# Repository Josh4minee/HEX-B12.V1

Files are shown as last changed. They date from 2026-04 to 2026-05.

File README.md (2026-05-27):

##
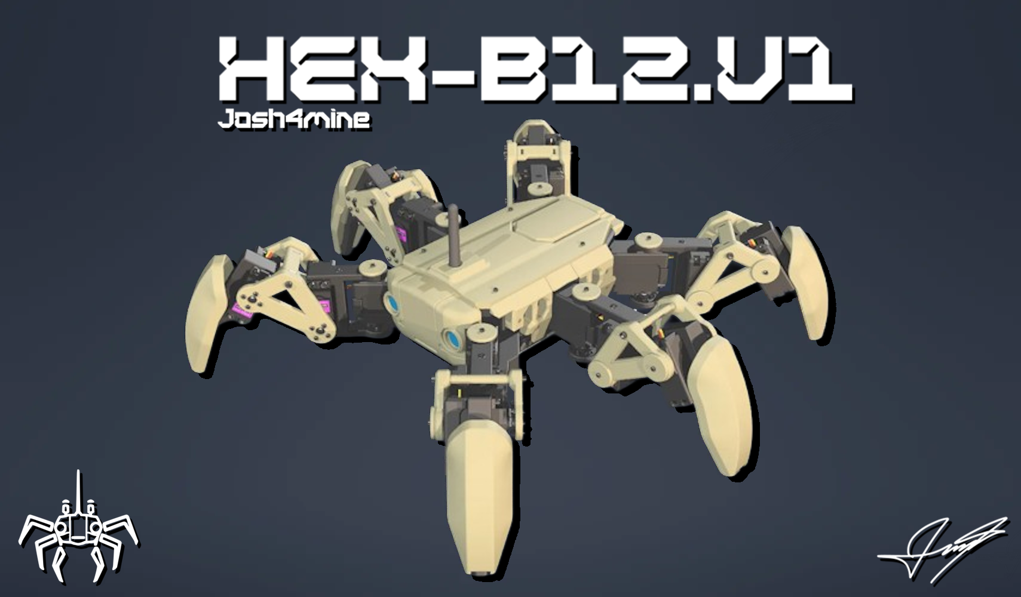
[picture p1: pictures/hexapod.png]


# HEX-B12.V1
HEX-B12.V120 is a custom-designed hexapod using MG996R servos. Its theme is based on the beloved bot B-12 from the popular video game [Stray](https://en.wikipedia.org/wiki/Stray_(video_game)). It is inspired by the Make Your Pet project and is powered by a custom inverse kinematics-based algorithm.

The mechanical part dimensions are inspired by the [Make Your Pet](https://www.makeyourpet.com/) Chipo project; everything else is custom-made by me.

# Information
Consult the following based on your needs:
- [Hexapod](#hexapod)
- [Remote](#remote)
- [Printing](#printing)
- [Wiring diagram](#wiring-diagram)
- [Hexapod Assembly](#hexapod-assembly)
- [Hexapod pictures and videos](#hexapod-pictures-and-videos)
- [Pre-powering on precautions](#pre-powering-on-precautions)
- [Remote Assembly](#remote-assembly)
- [How to use the remote](#how-to-use-the-remote)
- [Sources](#sources)
- [License](#license)

# Hexapod

Why I made this hexapod is because since I was young I have always wanted to build "stuff", making robots was always very appealing to me and this project is simpler than a quadruped yet just as fun for a beginner like me and I hope the people that come across this project like it! It is worth mentionning that this is also a college project hense why I have put so much time and effort on it in such a short ammount of time.

As per the title, this hexapod uses MG996R servos, this decision was made because of cost, any other servo is 3x to 4x the price of these ones.

The power system consists of one big 5200mAh 2S lipo battery for optimal opperation time, three UBECs for stable 7v to 5v conversion and one 10A manual reset fuse.

An arduino nano was used as the brains of this project simply because it was a requirement from my college and it is thanfully fast enough for its use case.

An [Adafruit PCA9685](https://learn.adafruit.com/16-channel-pwm-servo-driver/overview) servo driver was chosen to controll the huge amount fof servos this robot requires.

The nRF24L01+PA+LNA modules were chosen for wireless communication, the power emplified version was used for its antenna (to keep the resemblance of [B-12](https://stray.fandom.com/wiki/B-12)) and for its range.

Finally, relays were added for ease of use and safety, like only turning on the servos 5s after the battery is pluged in.

# Remote

The main reason the remote was made is because I did not want to work with bluetooth or web based control. 

Making a remote seemed more interesting anyways and it allowed me to design my very first custom PCB:

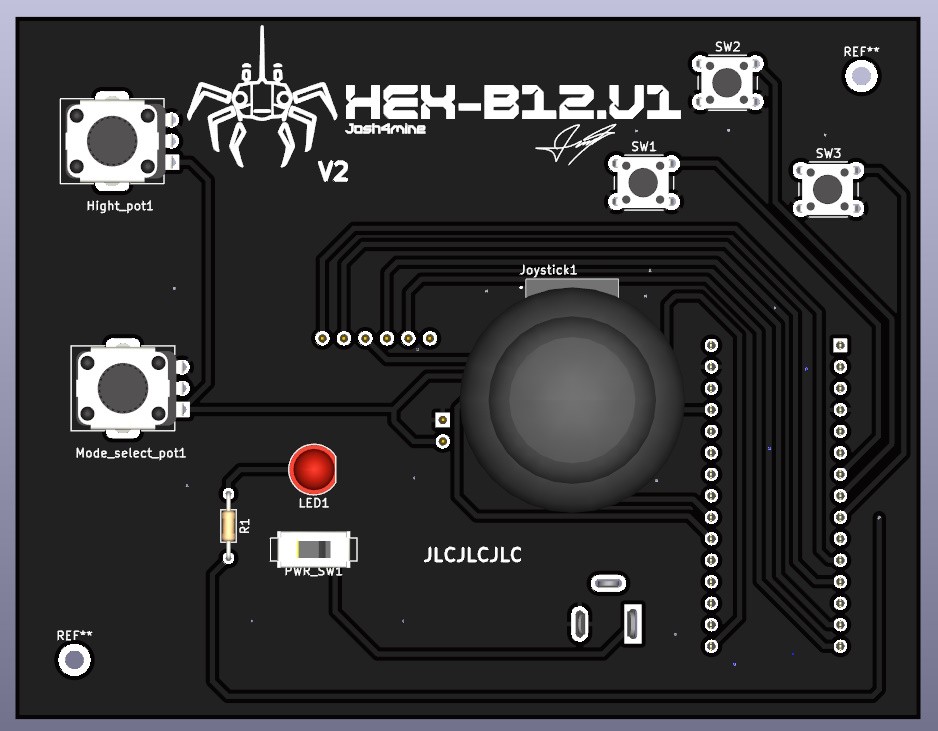
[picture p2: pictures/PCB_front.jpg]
  
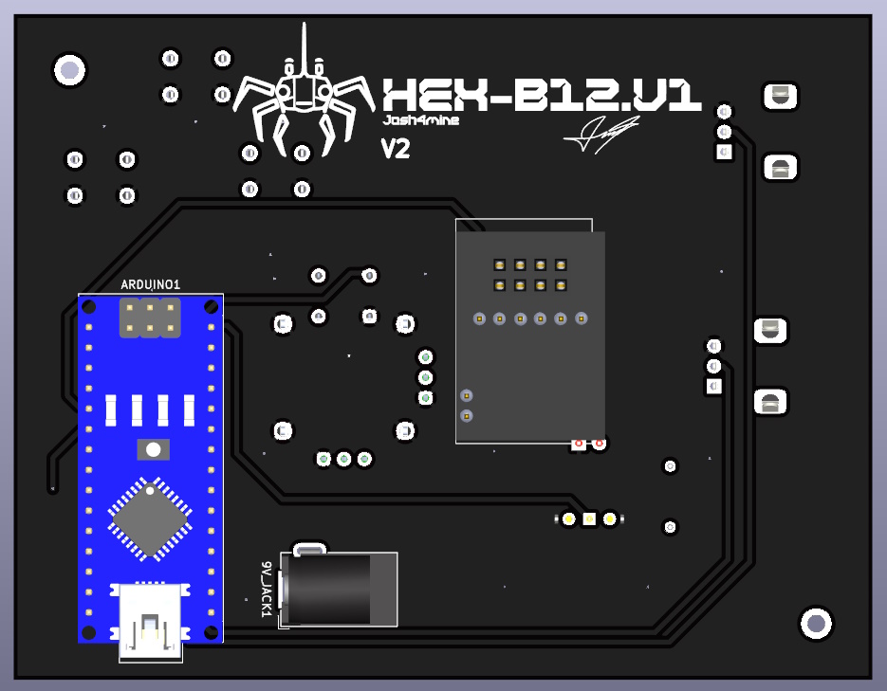
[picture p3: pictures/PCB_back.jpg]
  

I ended up making 2 versions because I tried to directly hook up an NRF module on the first version, this ended up failing to I just made a custom footprint for the NRF module power boards.

# Printing

The following are the settings used to print this hexapod:

- 15% grid infill everywhere, 0.28mm height and 3 walls on every part except for the 0.16mm servo shields to keep them smooth.
- Every STL file is pre-oriented and ready to print, the only parts requiring support material are the top plate, the shields, the coxa and femur horn parts, the guides. Any additional supports are not usefull.
- Printing the remote uses the same settings and the files are also pre-oriented, only the mid plate requires supports.
- The number of parts needed to be printed is indicated at the end of the names of every STL file.
- All STL files can be found the the [STL](./STL) folder.

# Wiring diagram

Here you can find the wiring diagram, component placements, and an IRL example of the completed build.
<div>
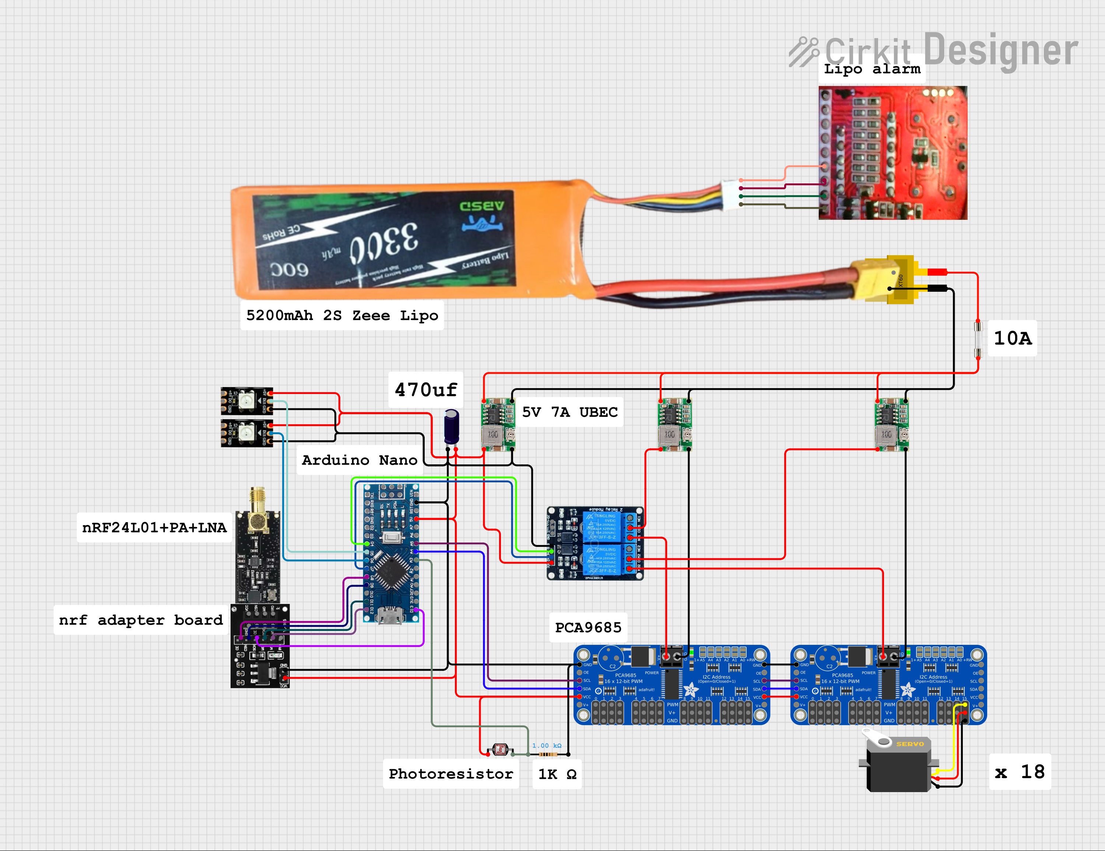
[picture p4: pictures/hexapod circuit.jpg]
  
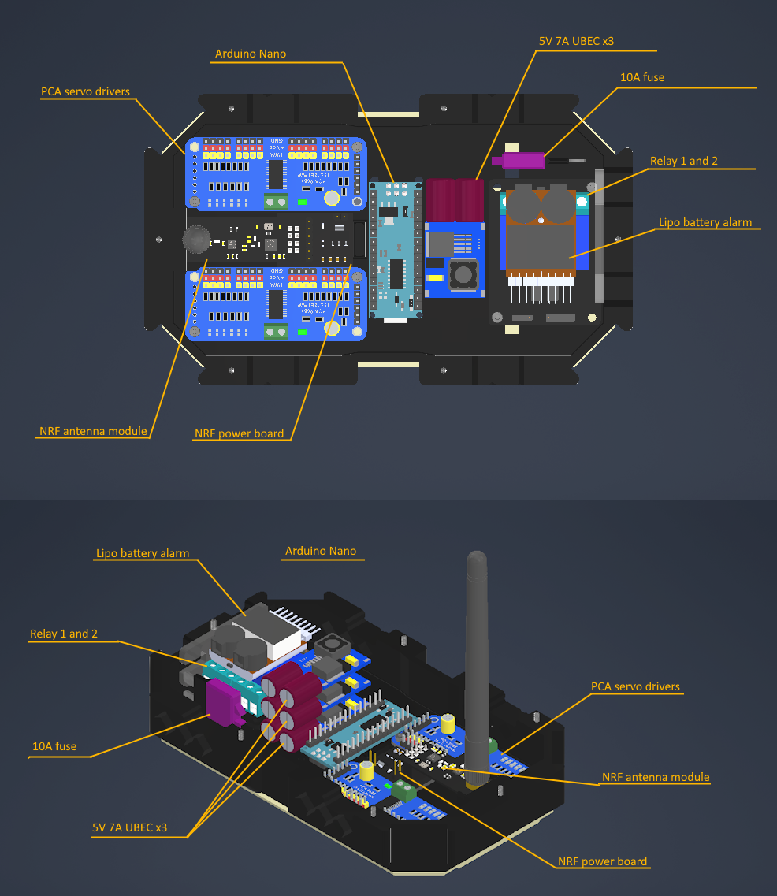
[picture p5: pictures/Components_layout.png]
  
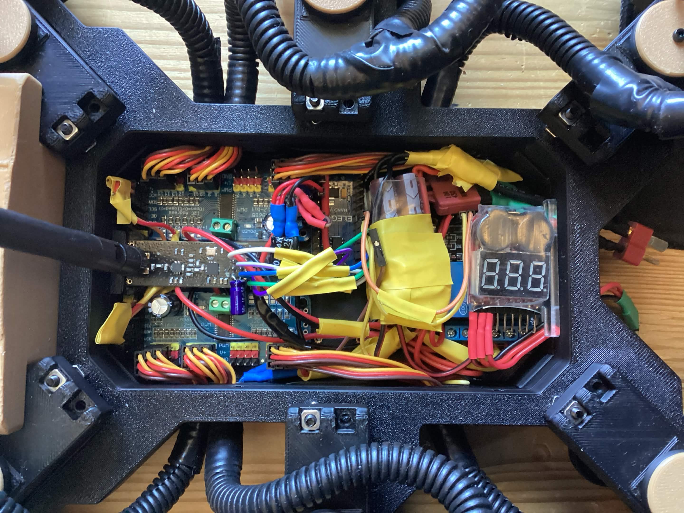
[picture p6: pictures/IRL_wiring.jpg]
  
<div>
  
# Hexapod assembly
- [Coxa](./pictures/coxa_page_1.jpg)
- [Femur](./pictures/femur_page_1.jpg)
- [Tibia](./pictures/tibia_page_1.jpg)
- [Leg](./pictures/LEG_left_page_1.jpg)
- [Mid Frame](./pictures/mid_frame_page_1.jpg)
- [Frame and Legs](./pictures/frampluslegs_page_1.jpg)
- [Hexapod](./pictures/hexapod_page_1.jpg)
- [Electronics Mounting](./pictures/electronics_mounting_page_1.jpg)
- [Servo pinouts](./pictures/servo_order.png)

**NOTE: ALL SERVOS MUST BE SET TO 90 PRIOR TO ANY ASSEMBLY**

**NOTE: KEEP IN MIND THAT 3 OF THESE LEGS ARE FLIPPED**

**NOTE: DO NOT FORGET THE 18 FRICTION CAP RINGS**

The above document provides a visual on how parts are assembled, to assemble this in real life you must follow the [Frame and Legs](./pictures/frampluslegs_page_1.jpg) and [Hexapod](./pictures/hexapod_page_1.jpg) technical drawings. The order of operations is very important here, so making sure proper understanding is acquired before continuing is mandatory.

For screw sizes needed:
- Every screw needed to attach a servo is M3 35mm.
- Every screw needed to clamp together femur/coxa parts is M3 25mm.
- Every screw that holds down the friction caps is M2 10mm.
- Every other screw is M2 8mm.
- Follow [this](./pictures/Hexapod_Heated_Insert_placements.png) diagram for M2 heat insert assembly.

Follow [this](./pictures/leg_orientations.png) technical drawing for proper leg orientation assembly.

It is very recommended to apply sillicone based grease between the friction caps and legs to prevent plastic wear.

# Hexapod pictures and videos

Here is what the robot should look like once fully assembled:
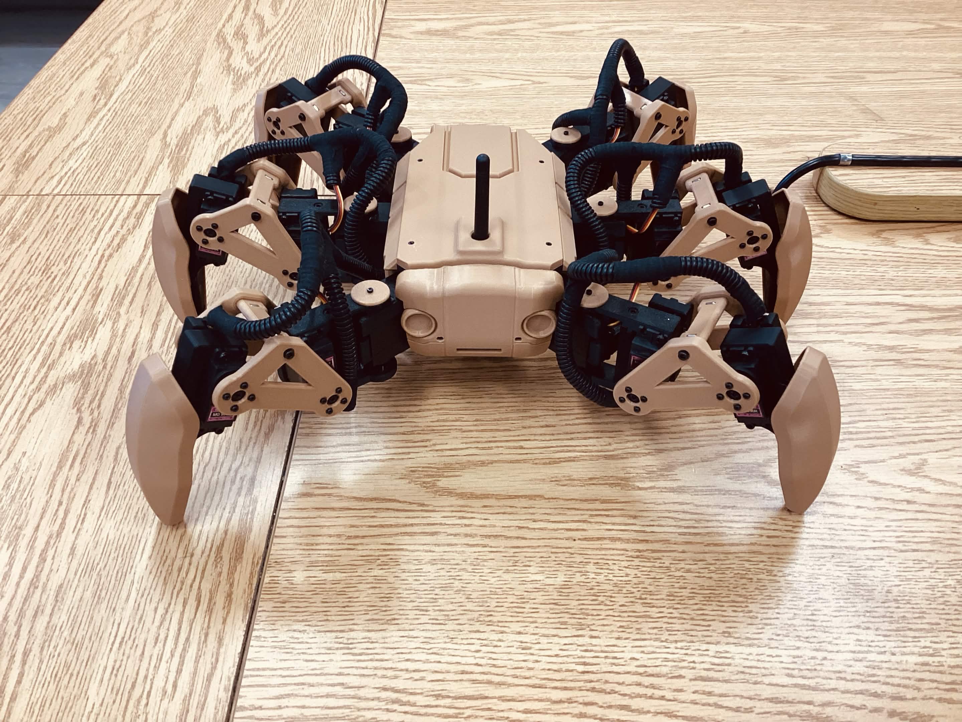
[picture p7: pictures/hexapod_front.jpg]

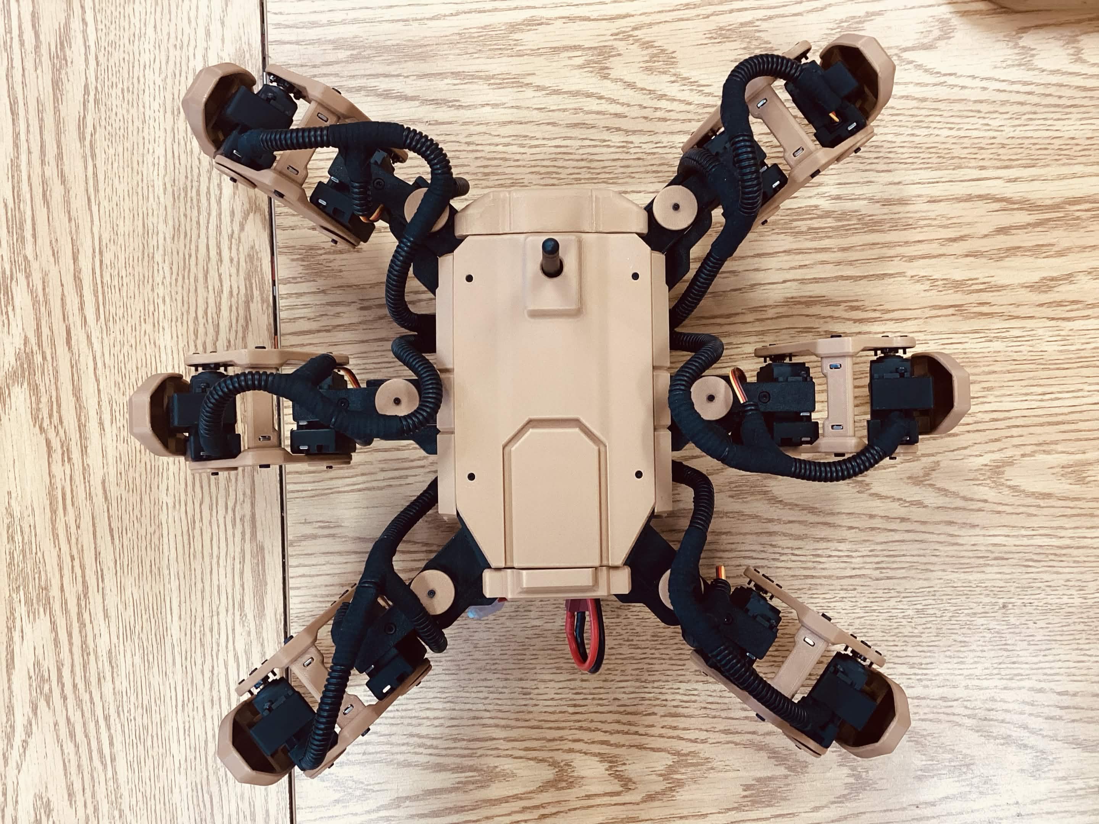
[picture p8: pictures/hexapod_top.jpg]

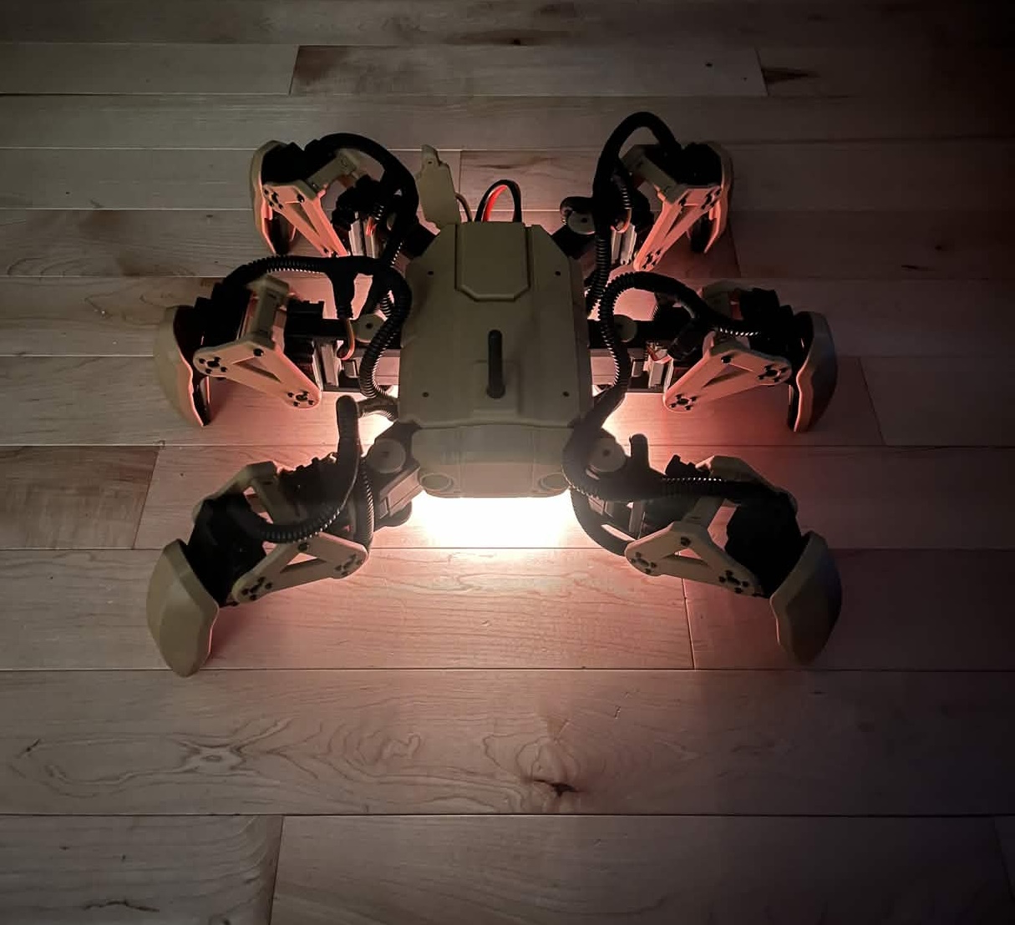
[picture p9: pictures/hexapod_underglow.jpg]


Here is what the remote should look like once fully assembled:
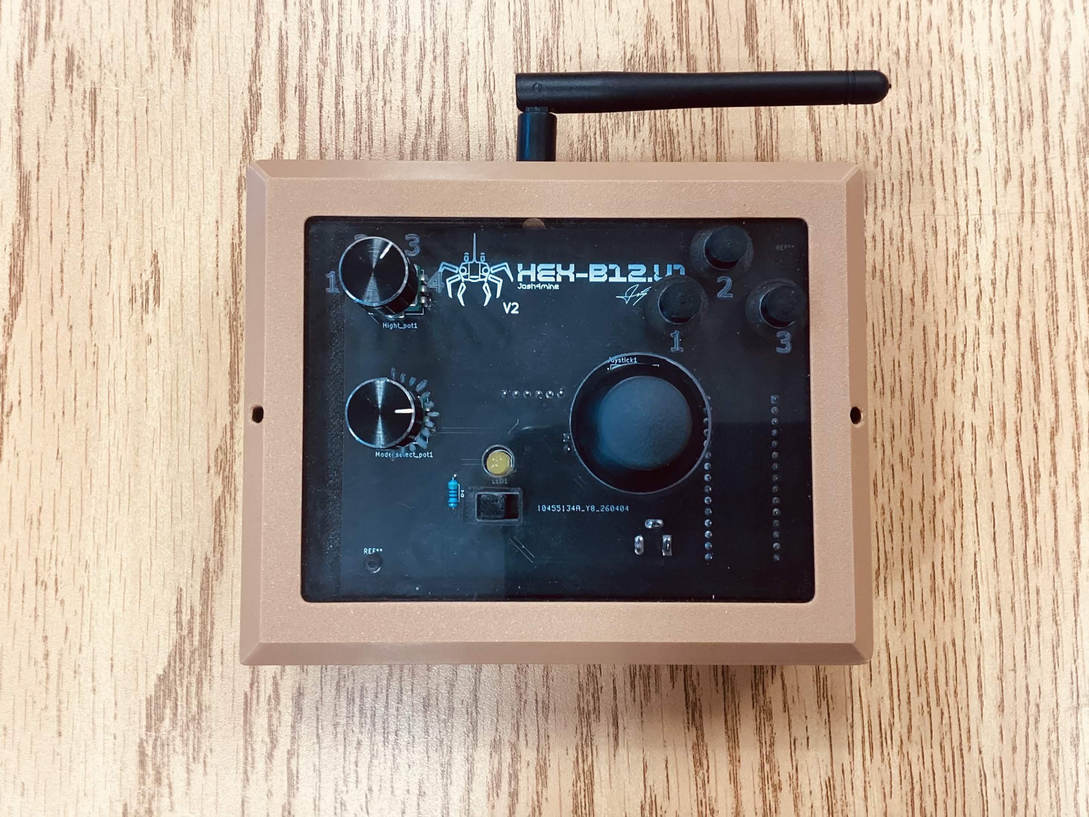
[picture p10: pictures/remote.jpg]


Here is a video demonstrating the functionalities of the hexapod:
<a href="https://www.youtube.com/watch?v=I4sm94-dwU4">
  
</a>
<video width="500" controls>
  <source src="hexapod.mp4" type="video/mp4">
</video>

# Pre-powering on precautions

- Make sure the legs of the hexapod are clear of any obstacles.
- Make sure all the legs are **RESTING** on the ground, the hexapod should **NOT** be standing.
- After plugging in the battery, the hexapod will enter a 10 second timer before entering its start animation.

# Remote assembly

Start by buying the PCB on [JLCPCB.](https://cart.jlcpcb.com/quote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) by simply drag and droping the [gerber](PCB/HEX_remote_GERBERS.zip) files.

Once you have received and soldered your PCB, follow the diagram to assemble the remote, every screw used is M2 8mm.

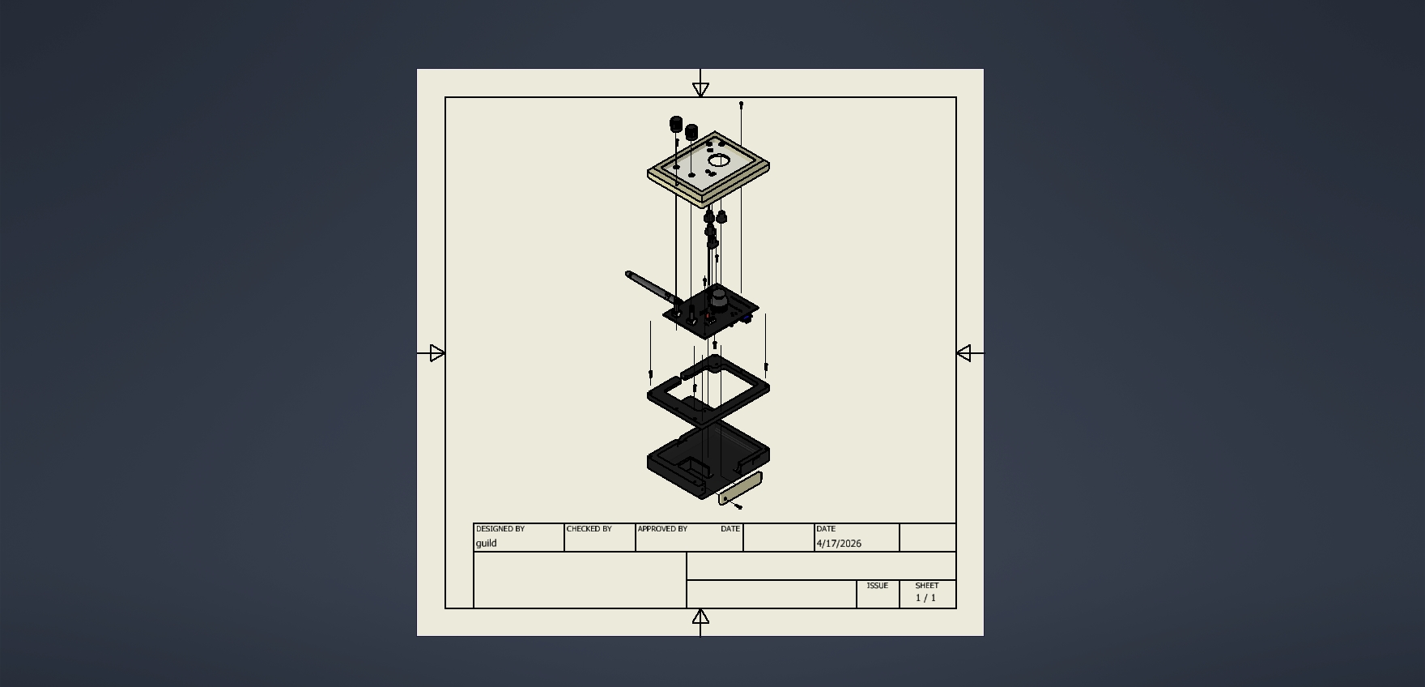
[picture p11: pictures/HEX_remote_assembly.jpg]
  

# How to use the remote

The remote has 3 buttons, 2 knobs, and a joystick.
The lower knob is for global height offset, the upper knob is used to control which mode the user is in, and the 3 buttons are for 3 different states in these modes:

- Normal walking mode: the hexapod turns and follows the joystick’s direction. Each button selects the current walking GAIT: 1 for tripod, 2 for ripple, and 3 is actually an Easter egg.

- Crab mode: the hexapod follows joystick directions without ever turning its body. The GAIT selection is the same as above.

- Body control mode: here you can control the hexapod body. Button 1 is for planar offset mode, button 2 is for XY rotation offset mode, and button 3 is for Z rotation mode.

- Animation mode: in this mode, 3 animations can be selected using the 3 buttons.

# Sources

Huge thanks to to [MYP](https://www.makeyourpet.com/) for the inspiration and just overall help their discord community provided to this project!

Here is a list of every model I used from GrabCad to display electronic components and screws in my assem,blies:

- [All M3-M2 screws](https://grabcad.com/library/m2-metric-socket-cap-head-screws-1)
- [M3 square nuts](https://www.traceparts.com/en/product/din-square-nut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)
- [NRF anttenna module and powe board](https://github.com/KrishnaHariharan/NRF24-Breakout-Board)
- [NRF anttenna module and powe board](https://github.com/Ahsayn/nRF24-Breakout)
- [MG996R servo & servo horns](https://grabcad.com/library/mg996r-servo-3)
- [UBEC](https://grabcad.com/library/ubec-5v-5a-1)
- [Lipo alarm](https://grabcad.com/library/1-8s-lipo-li-ion-fe-battery-voltage-2in1-tester-1)
- [PCA servo driver](https://grabcad.com/library/pca9685-8)
- [Double relay](https://grabcad.com/library/2ph63091a-2-channel-5v-relay-module-1)

# License
[License](LICENSE)

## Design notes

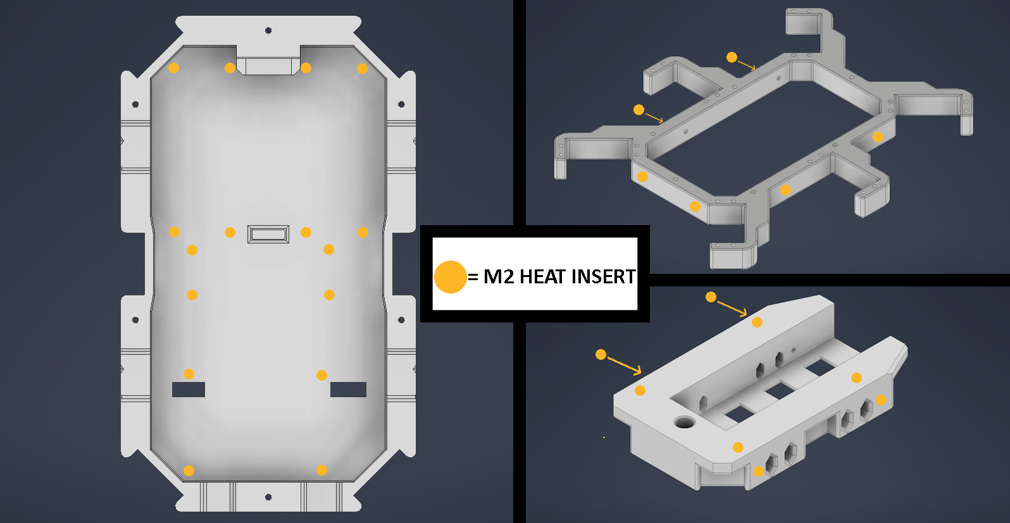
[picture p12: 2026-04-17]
pictures/Hexapod_Heated_Insert_placements.png

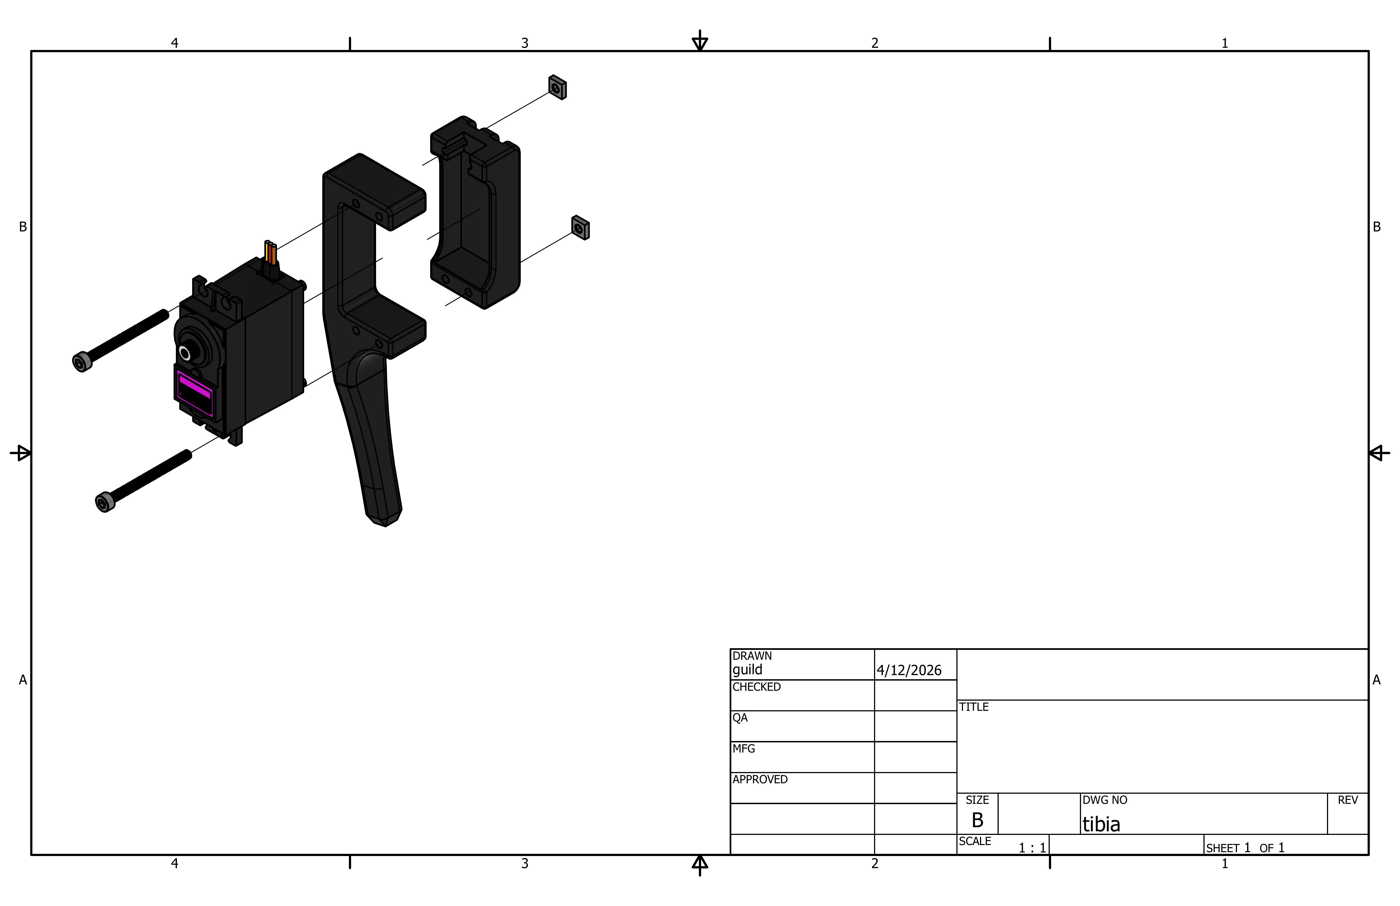
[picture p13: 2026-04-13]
pictures/tibia_page_1.jpg

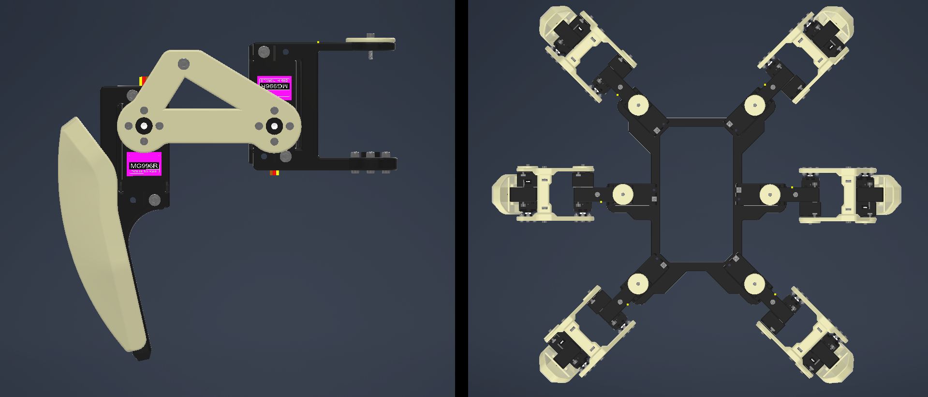
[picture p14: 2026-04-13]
pictures/leg_orientations.png

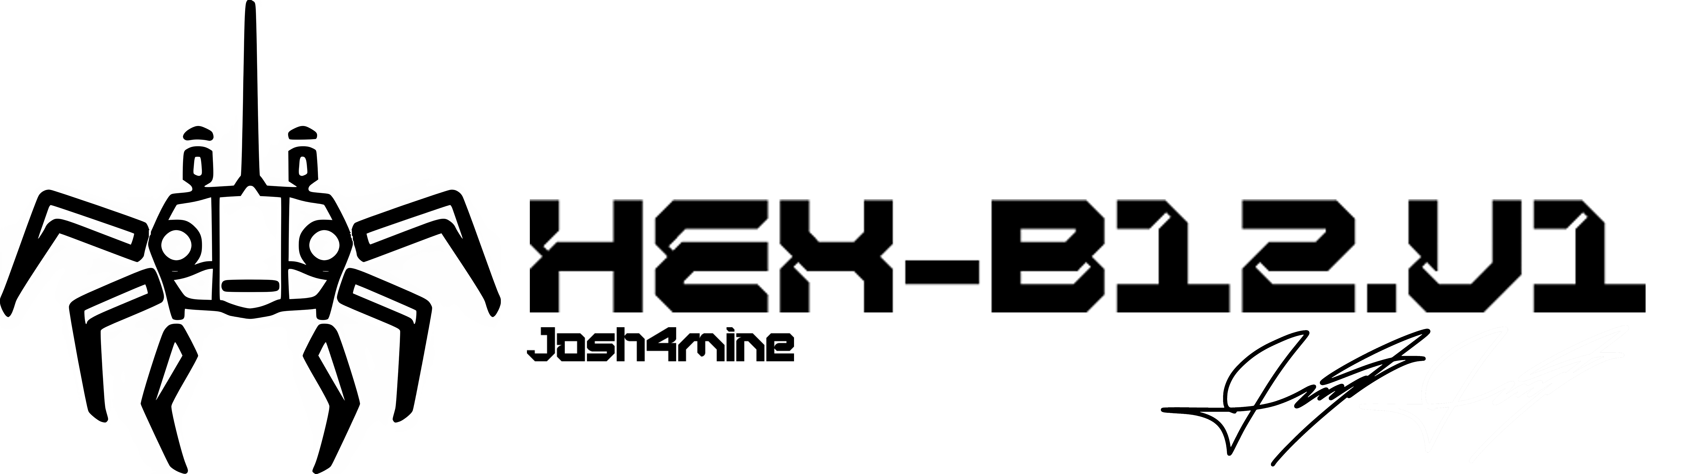
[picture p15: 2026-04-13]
pictures/HEX_sprite.png

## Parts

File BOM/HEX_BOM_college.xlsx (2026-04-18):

Part name | Used for | Link | Quantity | Price/Unit | Total
M2x10mm | Friction cap mounting | Aliexpress (https://www.aliexpress.com/item/32810872544.html) | get a 50 packs | 2.19 | $2.19
Zeee 2s Lipo 5200mA | Hexapod power | Amazon (https://www.amazon.ca/gp/product/B08B148D8S) | 1 |  | $28.99 | The Lipo on amazon is a two-pack for convenience but you can spend half for a single
Voniko 9V Batteries | Remote power | Amazon (https://www.amazon.ca/gp/product/B07RZ9PMQH) | 1 |  | $8.99
M2 locknuts | Servo & servo head mounting | Aliexpress (https://www.aliexpress.com/item/32798773566.html) | get the 50 pack twice |  | $14.82
M3 square nuts | Servo & servo head mounting | Aliexpress (https://www.aliexpress.com/item/1005001612157787.html) | get one 100 pack for each | $3.26 | $6.52
M2x8mm | Servo & servo head mounting | Aliexpress (https://www.aliexpress.com/item/32810872544.html) | get two 50 packs | 1.92 | $3.84
M3x25mm | Servo & servo head mounting | Aliexpress (https://www.aliexpress.com/item/32810872544.html) | get a 50 pack | 3.52 | 3.52
M3x35mm | Servo & servo head mounting | Aliexpress | get a 50 pack | 3.94 | 3.94
2x4 female Pin header | For the PCB NRF module | Aliexpress (https://www.aliexpress.com/item/33004522737.htm) | 1 |  | $2.81 | (comes in 2 pack)
T male plug | Connecting the Lipo to hexapod | Aliexpress (https://www.aliexpress.com/item/1005006840459578.html) | 1 |  | $2.72
9v Barrel jack | For powering PCB | Aliexpress (https://www.aliexpress.com/item/33005175186.html) | 1 |  | $2.45
RK097 B10k potentiometer | For PCB | Aliexpress (https://www.aliexpress.com/item/1005010063122061.html) | 1 |  | $2.95
1x6 90 degree male pin row | For servo controller | Aliexpress (https://www.aliexpress.com/item/1005007569841697.html) | 1 |  | $1.69
1x15 female pin header | For PCB arduino mounting | Aliexpress (https://www.aliexpress.com/item/4001198421663.html) | 1 |  | $2.63
10mm OD x 3m | For hexapod servo wires | Aliexpress (https://www.aliexpress.com/item/1005005188505524.html) | 1 |  | $5.25
SS12D00 SPDT 3 pin slide switch | Remote power switch | Aliexpress (https://www.aliexpress.com/item/1005007162182882.html) | 1 |  | $3.36
3 Modes Servo Tester Digital | For servo callibration | Aliexpress (https://www.aliexpress.com/item/1005002192090659.html) | 1 |  | $7.29
PCA9685PW 16 Channel controller | For servo control | Aliexpress (https://www.aliexpress.com/item/1005004959076770.html) | 2 | $3.69 | $7.38
NRF24L01+PA+LNA | Tranceiver module | Aliexpress (https://www.aliexpress.com/item/1005007038556192.html) | 2 | $4.73 | $9.46
1 Channel 5V Relay | Relay | Aliexpress (https://www.aliexpress.com/item/1005007010336494.html) | 2 | $4.29 | $8.59
Battery Low Alarm Buzzer | Rings when lipo is too low | Aliexpress (https://www.aliexpress.com/item/32723129432.html) | 1 |  | 3.19
NRF24L01 SOCKET | NRF PWR adapter soket | Aliexpress (https://www.aliexpress.com/item/1005005682218502.html) | 1 |  | $1.79
Arduino nano | Arduino nano | Aliexpress (https://www.aliexpress.com/item/1005006716897717.html) | 2 | $4.34 | $8.68
Capacitors (pack) | 10uf on NRF, 470uf on hexapod arduino | Aliexpress (https://www.aliexpress.com/item/1005009888050325.html) | 1 |  | 7.29
Joystick | Joystick for remote | Aliexpress (https://www.aliexpress.com/item/1005007344026383.html) | 1 |  | $1.76
6x6x5mm buttons | Buttons for remote | Aliexpress (https://www.aliexpress.com/item/4001166999847.html) | 1 |  | $2.17
5V 7A UBEC | For stable/usable Lipo voltage | Aliexpress (https://www.aliexpress.com/item/1005006414925607.html) | Pick the 2PCS 7A UBEC |  | $17.58
5V 3A UBEC (hexapod MCU boards) | For stable/usable Lipo voltage | Aliexpress (https://www.aliexpress.com/item/1005006414925607.html) | 1 |  | $6.99
16AWG tinned silicone wire | For hexapod wiring | Aliexpress (https://www.aliexpress.com/item/1005003058991433.html) | black/red pair, 1m |  | $12.58
22 AWG tinned silicone wire | For hexapod wiring | Aliexpress (https://www.aliexpress.com/item/1005003058991433.html) | black/red pair, 1m |  | $10.49
10c 40pcs FF dupont cable | For NRF on hexapod | Aliexpress (https://www.aliexpress.com/item/1005003641187997.html) | 1 |  | $2.52
1gk PLA spool | Can use any | Amazon (https://www.amazon.ca/dp/B09T2VFXL3) | 1, I will fund second colour |  | $22.99
Rubber tips for legs | ID must be 8mm or 5/16 inches | Aliexpress (https://www.aliexpress.com/item/1005004887472512.html) | 1 |  | $3.26
SMA female jack | SMA female front | Aliexpress (https://www.aliexpress.com/item/1005004242324252.html) | 1 |  | $1.91
MG996R servo motors (x16) | Alibaba is cheapest with 2 extra servos | Alibaba (https://www.aliexpress.com/item/1005004887472512.html) | 20 ( two packs of 10 ) | $2.91 | $58.04
Custom PCB | Remote | JLCPCB (https://cart.jlcpcb.com/quote) | 1 |  | $9.60
 |  |  |  | Additonal shipping is not calculated Aliexpress' is free anyways
 |  |  |  | Total: | $300.23 | Based on Canadian tax
 |  |  |  | GST | 5%
 |  |  |  | QST | 10%
 |  |  |  | After tax: | $345.26
 |  |  |  | 243.58$ USD

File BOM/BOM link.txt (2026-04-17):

https://docs.google.com/spreadsheets/d/1-J32MCZkha7sq0wtG9dT5nHZdrWovS9e/edit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

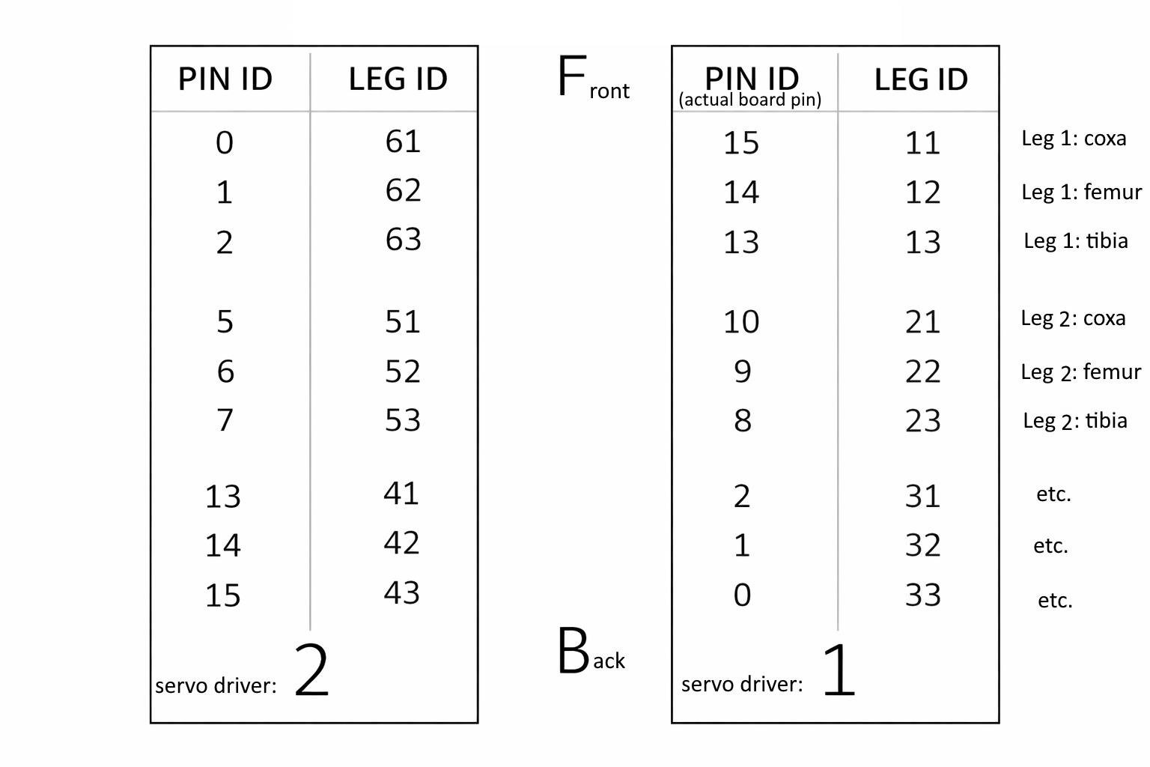
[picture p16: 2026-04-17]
pictures/servo_order.png

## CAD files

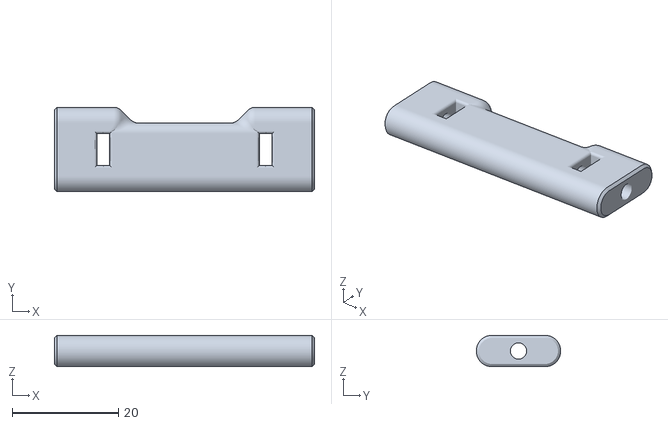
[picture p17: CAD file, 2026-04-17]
STL/Hexapod/femur_brace x6.stl
49.0 x 15.9 x 5.90

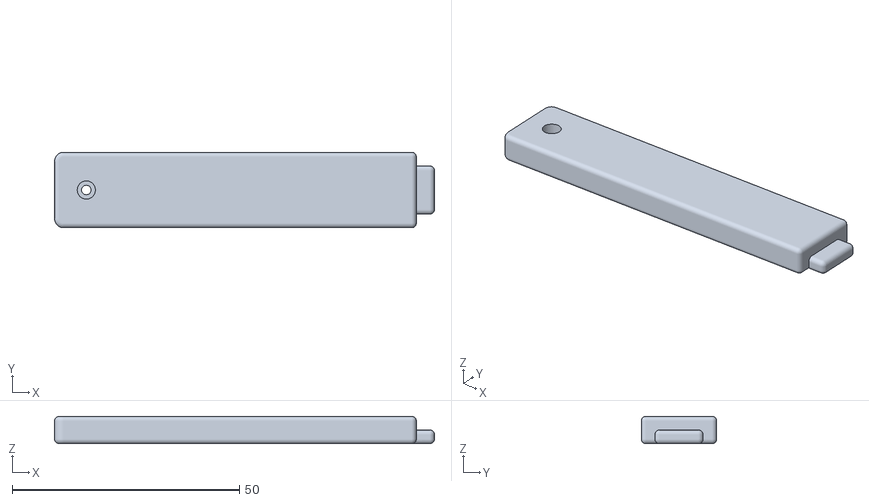
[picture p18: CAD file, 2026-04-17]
STL/Remote/battery cover x1.stl
83.6 x 16.6 x 6.00

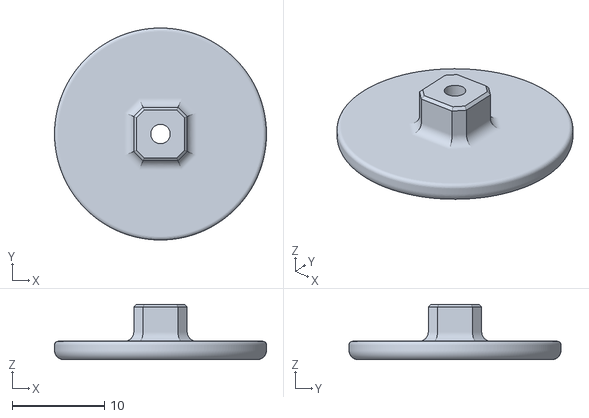
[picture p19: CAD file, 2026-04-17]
STL/Hexapod/friction cap x18.stl
23.0 x 23.0 x 6.00

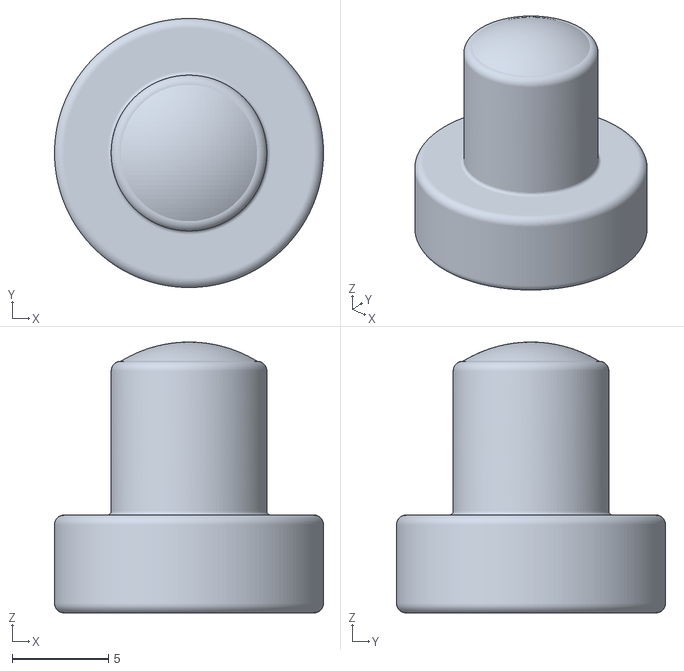
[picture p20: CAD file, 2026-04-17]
STL/Remote/remote button x3.stl
14.0 x 14.0 x 14.1

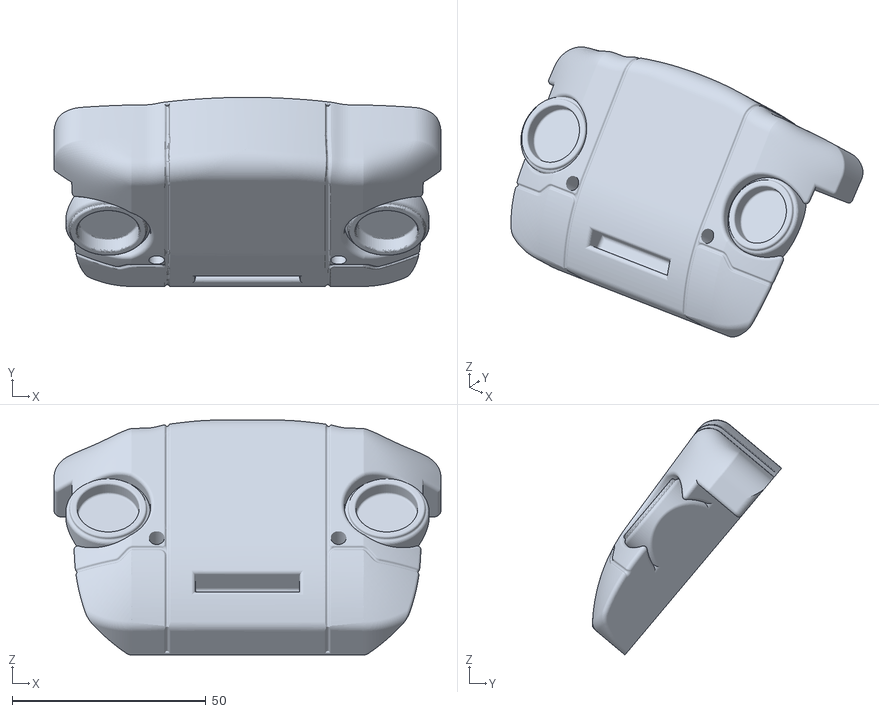
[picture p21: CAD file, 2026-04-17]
STL/Hexapod/face x1.stl
100.0 x 48.9 x 60.7

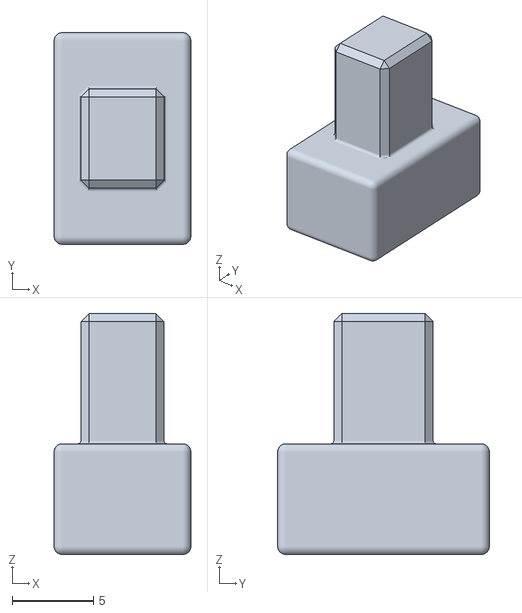
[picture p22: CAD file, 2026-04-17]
STL/Remote/remote switch x1.stl
8.40 x 13.0 x 14.8

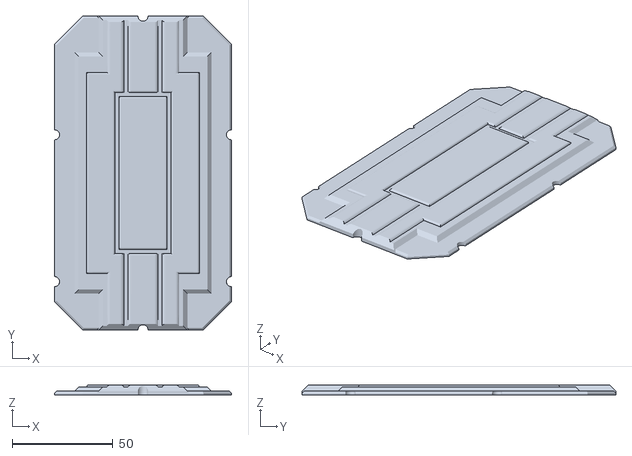
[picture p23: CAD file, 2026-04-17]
STL/Hexapod/bottom plate x1.stl
88.0 x 156.0 x 5.00

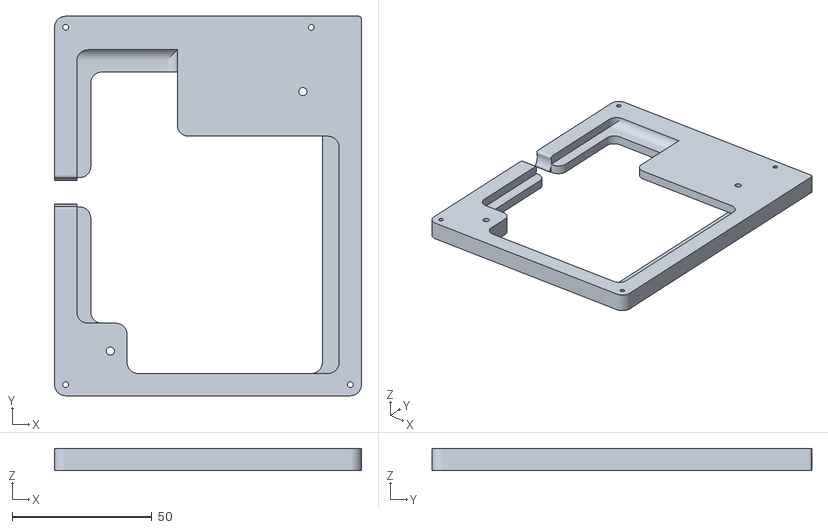
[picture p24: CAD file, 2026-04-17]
STL/Remote/rermote mid plate x1.stl
110.0 x 136.0 x 8.00

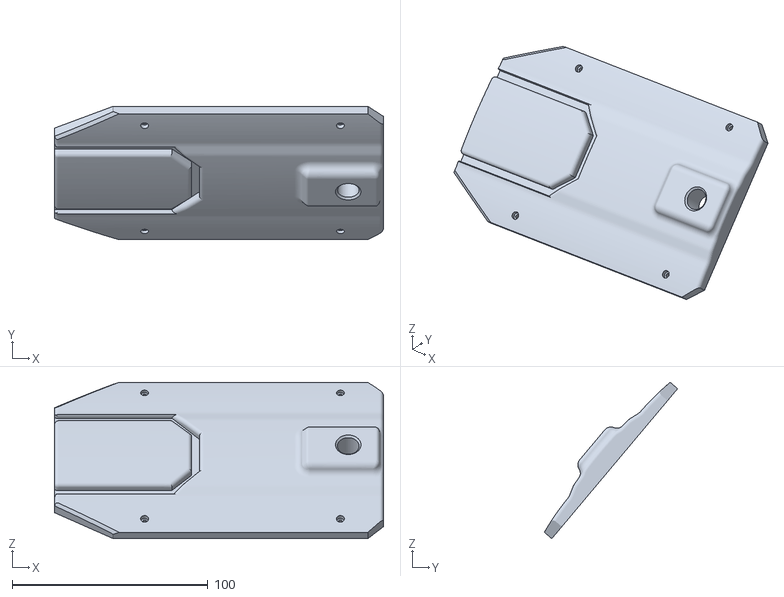
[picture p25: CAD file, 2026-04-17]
STL/Hexapod/top plate x1.stl
168.0 x 68.1 x 79.8

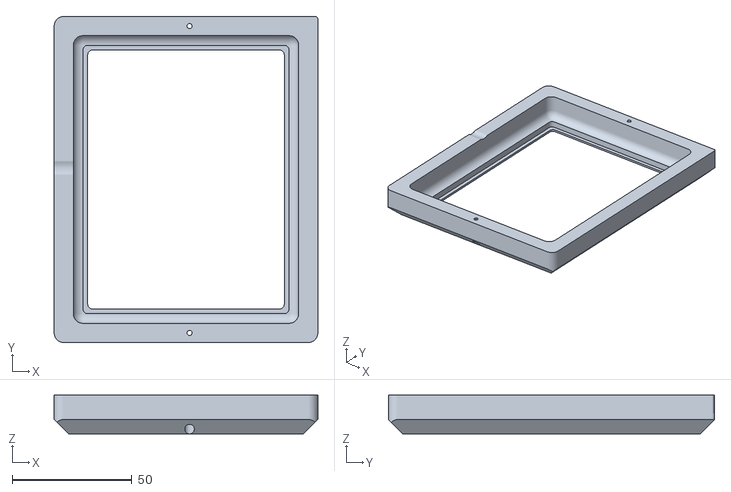
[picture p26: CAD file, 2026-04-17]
STL/Remote/remote top x1.stl
110.0 x 136.0 x 16.2

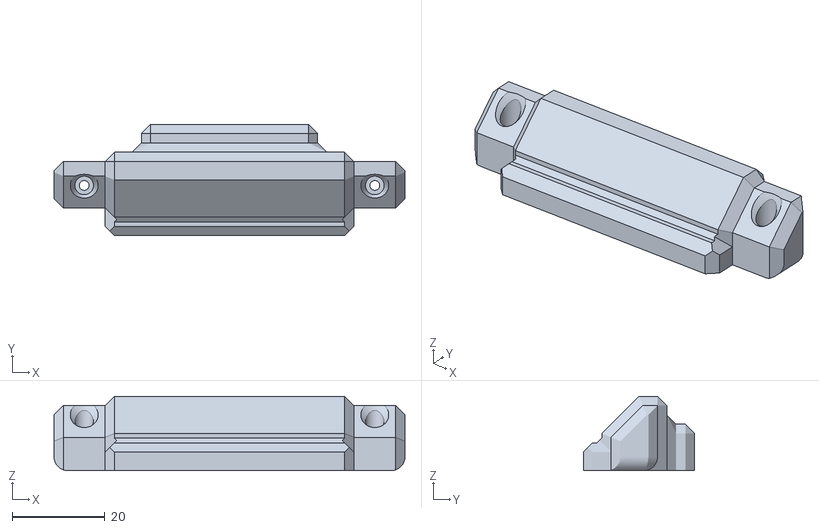
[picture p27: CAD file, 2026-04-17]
STL/Hexapod/back plate x1.stl
75.6 x 24.0 x 16.0

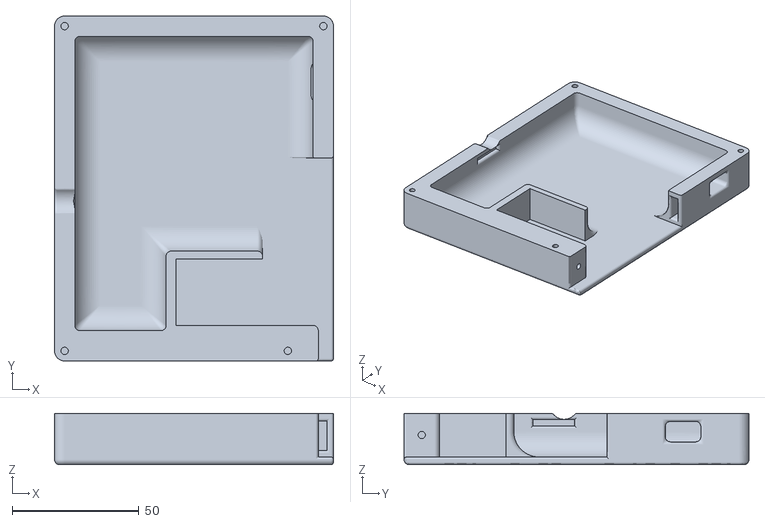
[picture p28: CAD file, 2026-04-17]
STL/Remote/remote base x1.stl
110.0 x 136.0 x 20.2

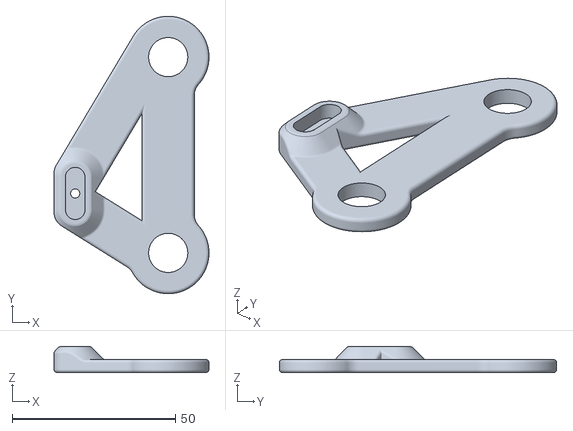
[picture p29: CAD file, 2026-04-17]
STL/Hexapod/femur_pegs x3.stl
47.5 x 85.0 x 8.00

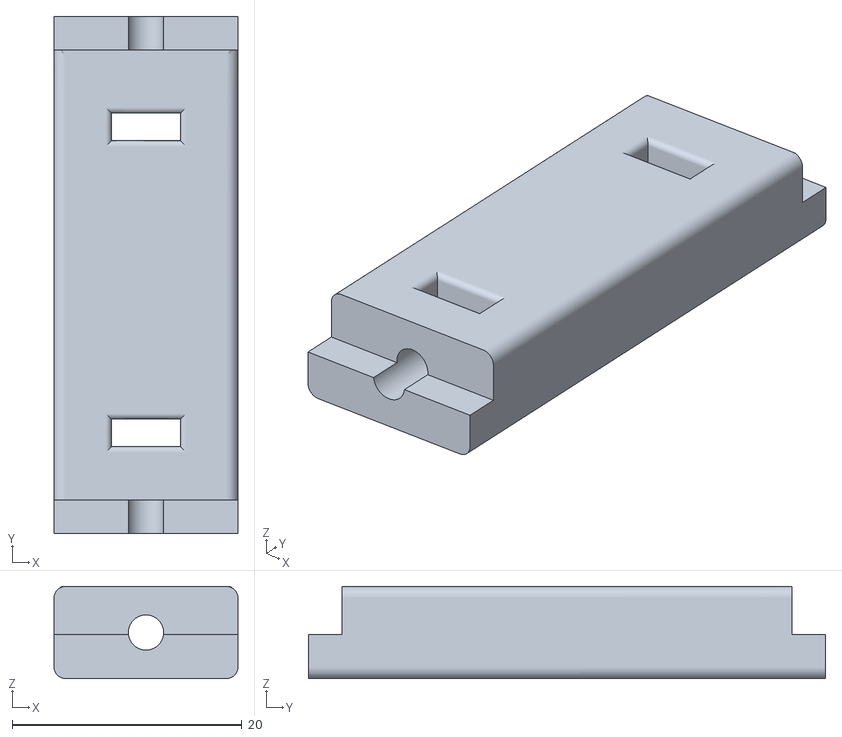
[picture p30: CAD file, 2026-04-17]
STL/Hexapod/coxa_brace x6.stl
16.0 x 45.0 x 8.00

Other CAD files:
STL/Hexapod/ring x18.stl
STL/Hexapod/side plate x1.stl
STL/Hexapod/coxa_horn x6.stl
STL/Hexapod/guide x18.stl
STL/Hexapod/bottom x1.stl
STL/Hexapod/coxa_peg x6.stl
STL/Hexapod/femur_horns x3.stl
STL/Hexapod/femur_horns_flipped x3.stl
STL/Hexapod/femur_pegs_flipped x3.stl
STL/Hexapod/frame x1.stl
STL/Hexapod/shield x6.stl
STL/Hexapod/side plate_flipped x1.stl
STL/Hexapod/tibia x6.stl
STL/Hexapod/top x1.stl

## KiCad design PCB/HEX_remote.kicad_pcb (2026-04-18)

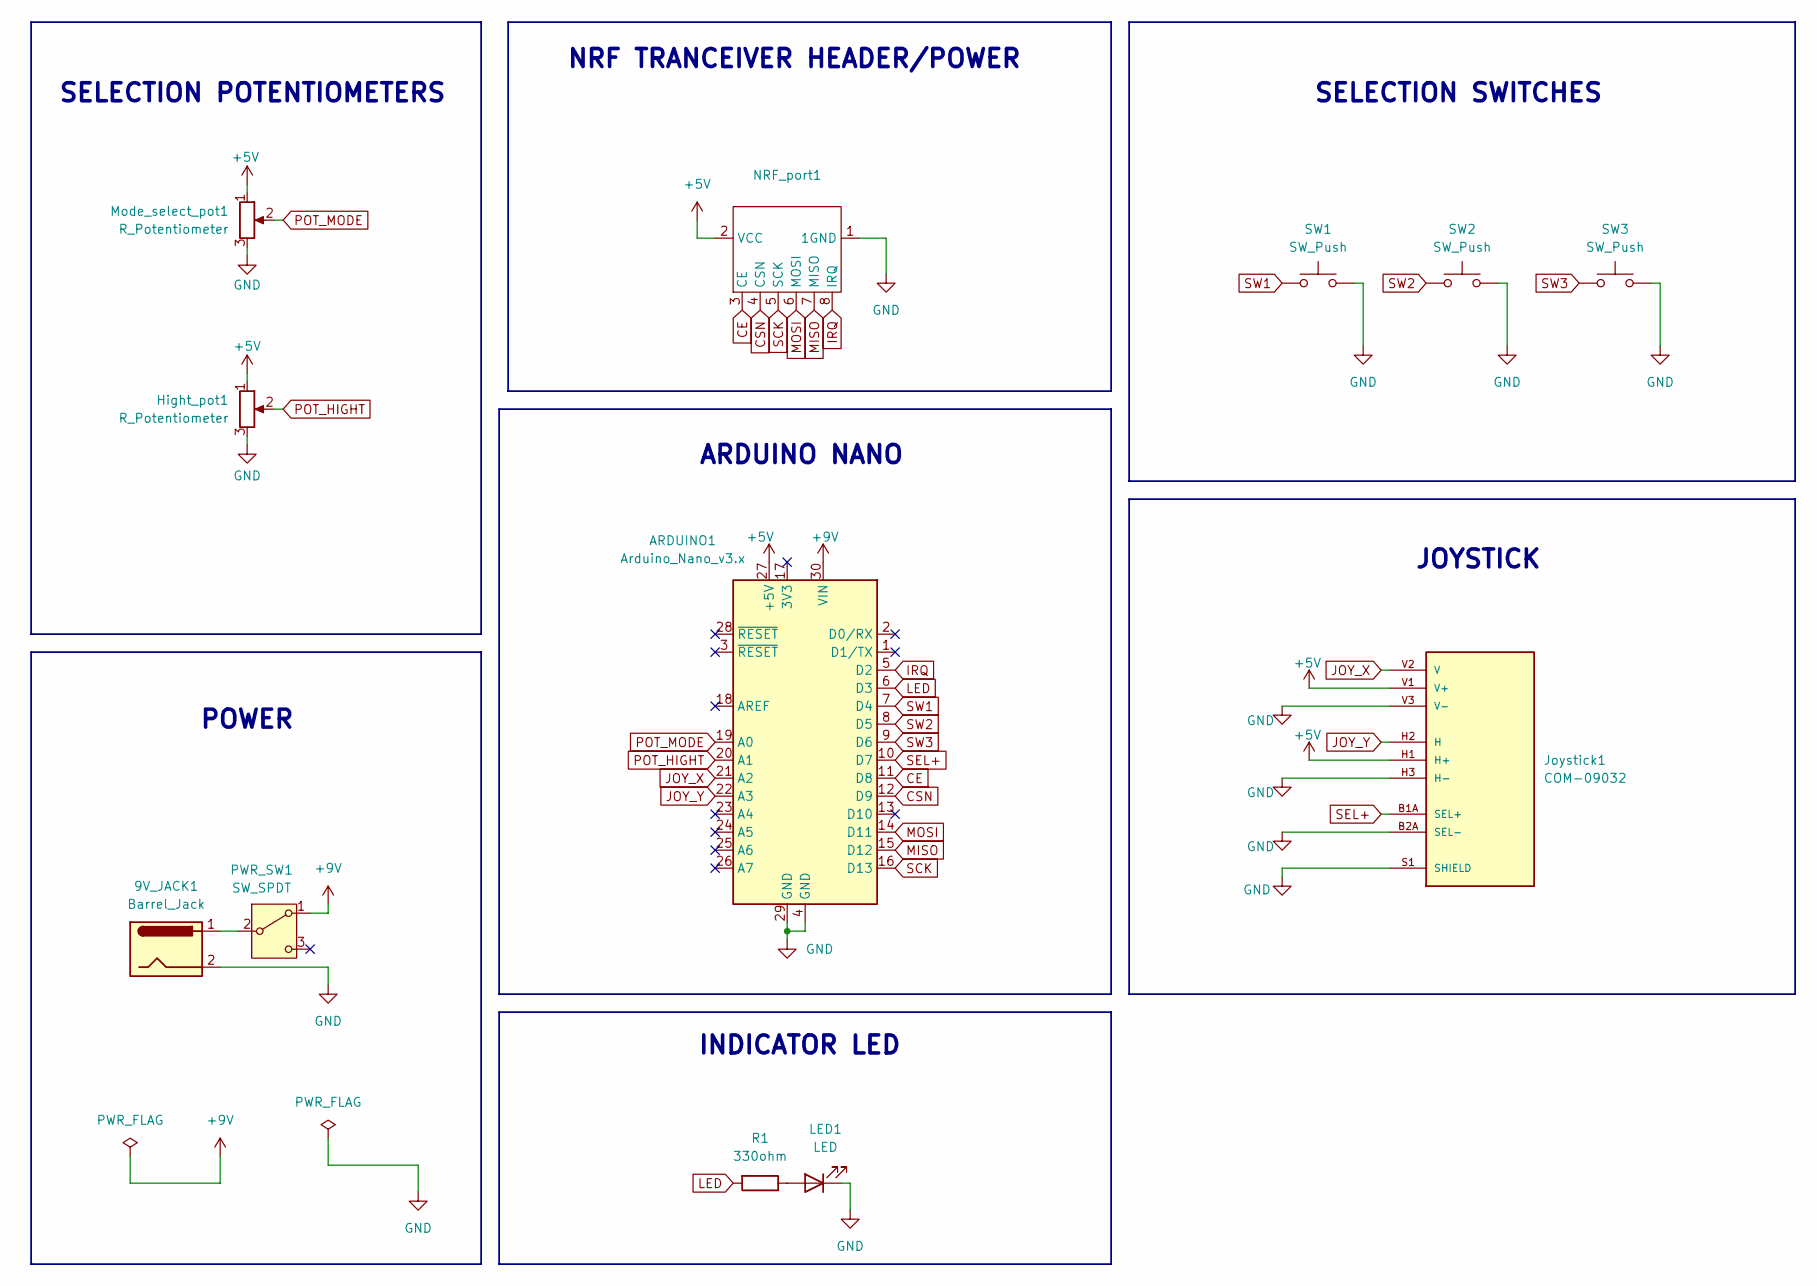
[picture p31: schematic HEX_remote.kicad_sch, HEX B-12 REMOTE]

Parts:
9V_JACK1: Barrel_Jack; BarrelJack_GCT_DCJ200-10-A_Horizontal
ARDUINO1: Arduino_Nano_v3.x; Arduino_Nano
Hight_pot1: R_Potentiometer; Potentiometer_Alps_RK09K_Single_Vertical
Joystick1: COM-09032; XDCR_COM-09032; PARTREV N/A
LED1: LED; LED_D5.0mm
Mode_select_pot1: R_Potentiometer; Potentiometer_Alps_RK09K_Single_Vertical
NRF_port1: NRF_ADAPTER_FOOTPRINT
PWR_SW1: SW_SPDT; SW_Slide-03_Wuerth-WS-SLTV_10x2.5x6.4_P2.54mm
R1: 330ohm; R_Axial_DIN0204_L3.6mm_D1.6mm_P7.62mm_Horizontal
SW1, SW2, SW3: SW_Push; SW_PUSH_6mm

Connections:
+5V: ARDUINO1.27 (+5V), Hight_pot1.1, Joystick1.H1 (H+), Joystick1.V1 (V+), Mode_select_pot1.1, NRF_port1.2 (VCC)
+9V: ARDUINO1.30 (VIN), PWR_SW1.1 (A)
CE: ARDUINO1.11 (D8), NRF_port1.3 (CE)
CSN: ARDUINO1.12 (D9), NRF_port1.4 (CSN)
GND: 9V_JACK1.2, ARDUINO1.4 (GND), ARDUINO1.29 (GND), Hight_pot1.3, Joystick1.B2A (SEL-), Joystick1.H3 (H-), Joystick1.S1 (SHIELD), Joystick1.S2 (SHIELD), Joystick1.S3 (SHIELD), Joystick1.S4 (SHIELD), Joystick1.V3 (V-), LED1.1 (K), Mode_select_pot1.3, NRF_port1.1 (1GND), SW1.2, SW2.2, SW3.2
IRQ: ARDUINO1.5 (D2), NRF_port1.8 (IRQ)
JOY_X: ARDUINO1.21 (A2), Joystick1.V2 (V)
JOY_Y: ARDUINO1.22 (A3), Joystick1.H2 (H)
LED: ARDUINO1.6 (D3), R1.2
MISO: ARDUINO1.15 (D12), NRF_port1.7 (MISO)
MOSI: ARDUINO1.14 (D11), NRF_port1.6 (MOSI)
unnamed: LED1.2 (A), R1.1
unnamed: 9V_JACK1.1, PWR_SW1.2 (B)
POT_HIGHT: ARDUINO1.20 (A1), Hight_pot1.2
POT_MODE: ARDUINO1.19 (A0), Mode_select_pot1.2
SCK: ARDUINO1.16 (D13), NRF_port1.5 (SCK)
SEL+: ARDUINO1.10 (D7), Joystick1.B1A (SEL+)
SW1: ARDUINO1.7 (D4), SW1.1
SW2: ARDUINO1.8 (D5), SW2.1
SW3: ARDUINO1.9 (D6), SW3.1

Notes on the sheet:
SELECTION SWITCHES
NRF TRANCEIVER HEADER/POWER
SELECTION POTENTIOMETERS
ARDUINO NANO
JOYSTICK
POWER
INDICATOR LED

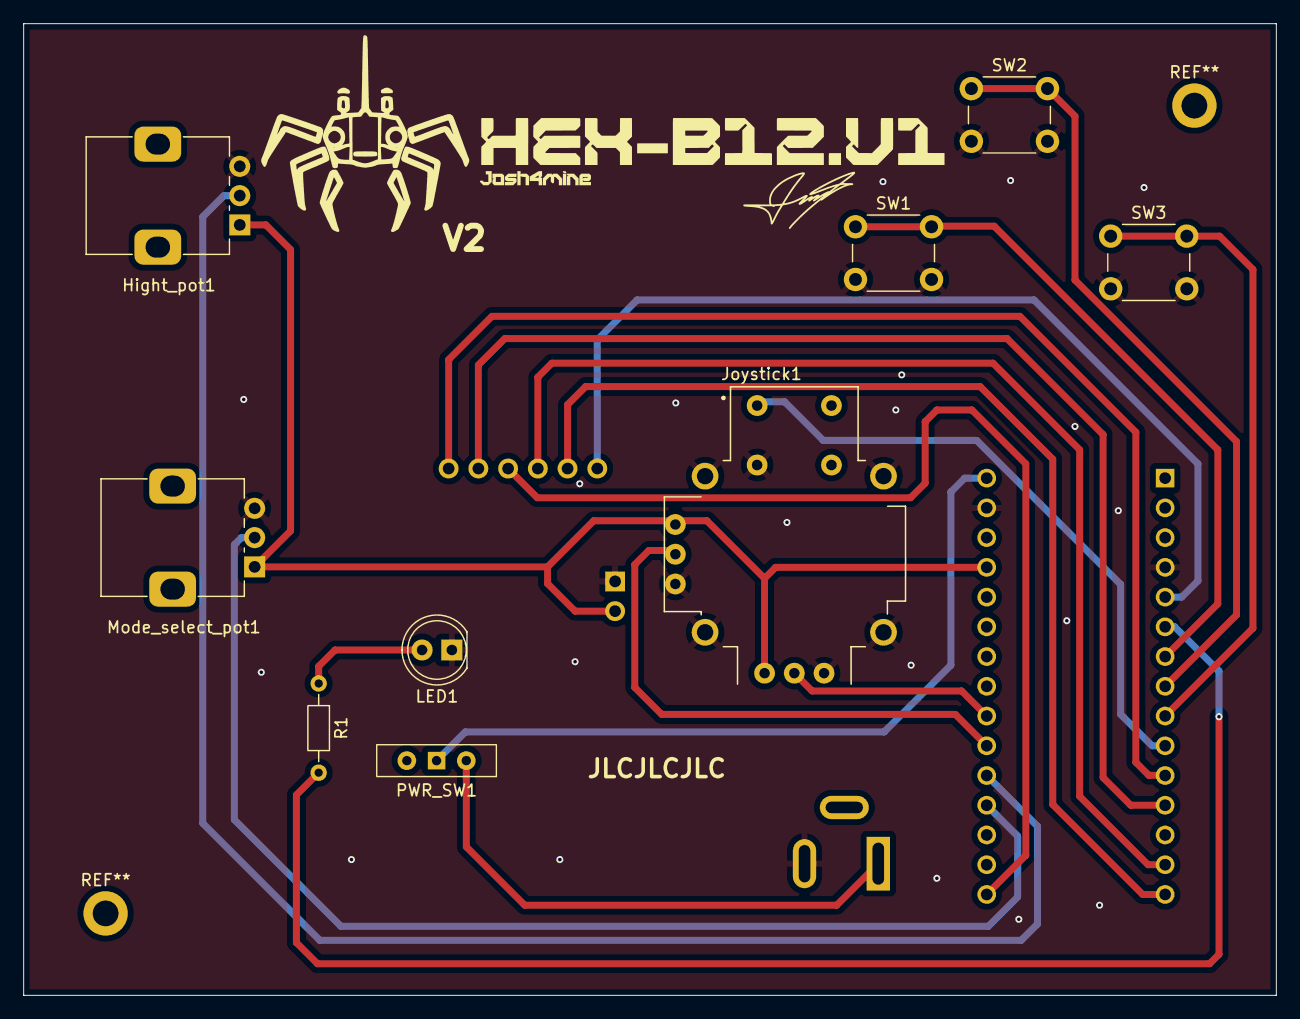
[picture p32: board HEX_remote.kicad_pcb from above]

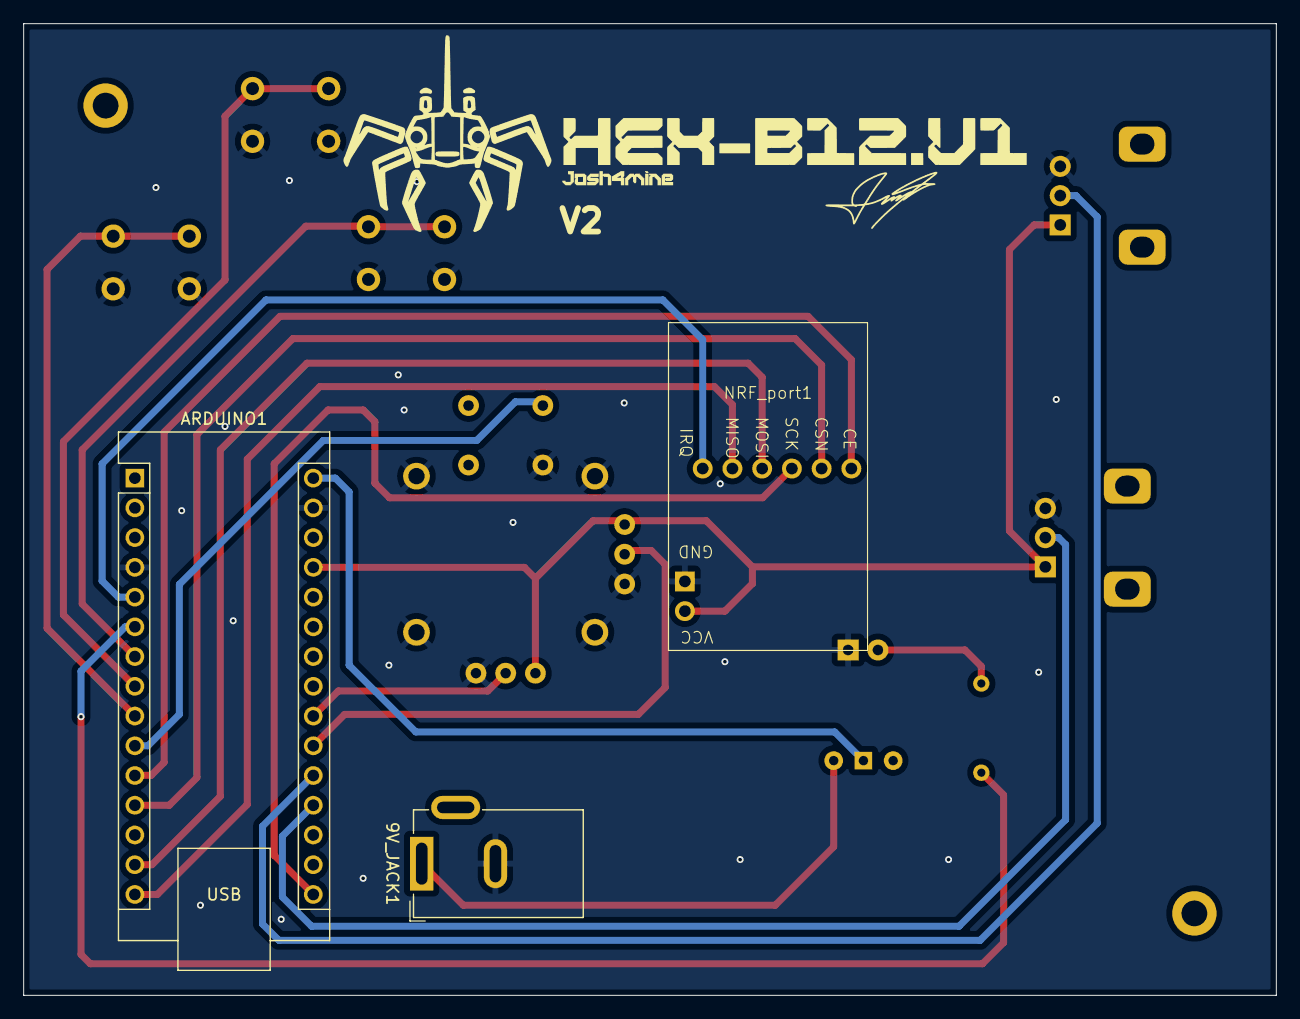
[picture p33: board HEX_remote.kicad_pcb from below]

Board: 2 copper layers, 107.0 x 83.0 mm, 12 parts (2 on the bottom side), 20 nets.

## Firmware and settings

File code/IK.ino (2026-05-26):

#include <SPI.h>
#include <nRF24L01.h>
#include <RF24.h>
#include <math.h>
#include <Wire.h>
#include <Adafruit_PWMServoDriver.h>
#include <FastLED.h>

bool START = true;

const float a = 60.0; //femur
const float b = 107.0; //tibia
const float l = 44.0; //coxa

const int relay1 = 4;
const int relay2 = 7;

CRGB leds1[5];
CRGB leds2[5];

int light;

Adafruit_PWMServoDriver pwm1 = Adafruit_PWMServoDriver(0x40);
Adafruit_PWMServoDriver pwm2 = Adafruit_PWMServoDriver(0x41);

int minPulses[18] = {113, 97, 130, 118, 87, 126, 105, 101, 117, 125, 113, 117, 126, 117, 117, 89, 134, 122};
int maxPulses[18] = {518, 502, 535, 523, 492, 531, 510, 506, 522, 530, 518, 522, 531, 522, 522, 494, 539, 527};

int pointsX[] = {175, 210, 175, -175, -210, -175};
int pointsY[] = {175, 0, -175, -175, 0, 175};

//------------------------------------------------------GAITs---------------------------------------------------------

int GAIT[3][8] = {
  {0, 0, 0, 0, 0, 0, 4, 4},   // Tripod
  {0, 0, 0, 0, 0, 0, 4, 4},    // Wave
  {0, 0, 0, 0, 0, 0, 4, 4}       // Ripple
};

//---------------------------------------------------Mode2 Variables--------------------------------------------------

unsigned long lastStep[6] = {0};
unsigned long stepDelay = 20;

int lastOption = 0;
int lastMode = 3;
int state[6];
int i[6];

//---------------------------------------------------receiverSetup----------------------------------------------------

RF24 radio(8, 9); // CE, CSN

const byte address[6] = "00001";

unsigned long lastReceiveTime = 0;
unsigned long currentTime = 0;

struct Data_Package { // data package sent to hexapod
  byte mode;
  byte height;
  byte joystick_x;
  byte joystick_y;
  byte joystick_select;
  byte option;
};
Data_Package data; //Create a variable with the above structure

//-------------------------------------------------------SETUP---------------------------------------------------------
void setup()
{
  Serial.begin(9600);
  
  //enable PCA servo drivers
  pwm1.begin();
  pwm2.begin();
  pwm1.setPWMFreq(50);
  pwm2.setPWMFreq(50);
  yield();

  //enable relays
  pinMode(4, OUTPUT);
  pinMode(7, OUTPUT);
  digitalWrite(4, LOW);
  digitalWrite(7, LOW);

  radio.begin();                                 //----NRF transmission setup
  radio.openReadingPipe(0, address);
  radio.setPALevel(RF24_PA_LOW);
  radio.startListening();

  
  FastLED.addLeds<WS2812B, 5, GRB>(leds1, 5); //-----LED setup
  FastLED.addLeds<WS2812B, 6, GRB>(leds2, 5);
  FastLED.setMaxPowerInVoltsAndMilliamps(5, 500);
  FastLED.setBrightness(60);
  FastLED.clear();
  FastLED.show();
}


//-------------------------------------------------------LOOP----------------------------------------------------------
void loop()
{
  if(START == true){
  startAnim();
  START = false;
  }

  if (radio.available())
  {
    radio.read(&data, sizeof(Data_Package));

    // Debug print
    //Serial.print("Mode: "); Serial.println(data.mode);
    //Serial.print("Height: "); Serial.println(data.height);
    //Serial.print("Joy X: "); Serial.println(data.joystick_x);
    //Serial.print("Joy Y: "); Serial.println(data.joystick_y);
    //Serial.print("Joy Btn: "); Serial.println(data.joystick_select);
    //Serial.print("Option: "); Serial.println(data.option);
  }
  
  light = analogRead(A3); // LED check
  if (light < 15) {
    for (int i = 0; i < 5; i++) {
      leds1[i] = CRGB(255, 110, 0);
      leds2[i] = CRGB(255, 110, 0);
      FastLED.show();
    }
  }
  else {
    for (int i = 0; i < 5; i++) {
      leds1[i] = CRGB(0, 0, 0);
      leds2[i] = CRGB(0, 0, 0);
      FastLED.show();
    }
  }

  switch(data.mode)
  {
    case 1: mode1(); break;
    case 2: mode2(); break;
    case 3: mode3(); break;
    case 4: mode4(); break;
  }
}

int mode1(){ // in development

}

int mode2() {
  if (data.option != lastOption) // checks for previous cycle
  lastMode = 0;
  lastOption = data.option;

  if (lastMode != 2) {
    state[0] = 1; i[0] = GAIT[data.option - 1][0]; // call selected GAIT
    state[1] = 2; i[1] = GAIT[data.option - 1][1];
    state[2] = 1; i[2] = GAIT[data.option - 1][2];
    state[3] = 2; i[3] = GAIT[data.option - 1][3];
    state[4] = 1; i[4] = GAIT[data.option - 1][4];
    state[5] = 2; i[5] = GAIT[data.option - 1][5];
    lastMode = 2;
  }

  legSwingC(1); // call leg swing
  legSwingC(2);
  legSwingC(3);
  legSwingC(4);
  legSwingC(5);
  legSwingC(6);
}

int mode3(){
  switch(data.option){
    case 1: {
      int H = map(data.height, 0, 255, 30, -30);       // option one, translation math
      int X = map(data.joystick_y, 0, 255, 40, -40);
      int Y = map(data.joystick_x, 0, 255, 40, -40);
      IK(175 + X, 175 + Y, -70 + H, 1);
      IK(210 + X,   0 + Y, -70 + H, 2);
      IK(175 + X, -175 + Y, -70 + H, 3);
      IK(-175 + X,-175 + Y, -70 + H, 4);
      IK(-210 + X,  0 + Y, -70 + H, 5);
      IK(-175 + X, 175 + Y, -70 + H, 6);
    break;
    }
    case 2: {
      int H = map(data.height, 0, 255, 30, -30);       // option one, Z rotation math
      float angle = map(data.joystick_y, 0, 255, 25, -25) * PI / 180.0;
      for(int i = 0; i < 6; i++){
        int X = pointsX[i];
        int Y = pointsY[i];
        int XR = X*cos(angle) - Y*sin(angle);
        int YR = X*sin(angle) + Y*cos(angle);
        IK(XR, YR, -70 + H, i+1);
      }
    break;
    }
    case 3: {
      int H = map(data.height, 0, 255, 0, -15);          // option one, X and Y dual rotation math
      float angleX = map(data.joystick_y, 0, 255, -10, 10) * PI / 180.0;
      float angleY = map(data.joystick_x, 0, 255, -10, 10) * PI / 180.0;
      for(int i = 0; i < 6; i++){
        int X = pointsX[i];
        int Y = pointsY[i];
        int Z = -70;

        int XR = X*cos(angleX) - Z*sin(angleX); //first rotation
        int ZR = X*sin(angleX) + Z*cos(angleX);

        int YR = Y*cos(angleY) - ZR*sin(angleY); //second rotation
        Z = Y*sin(angleY) + ZR*cos(angleY);

        IK(XR, YR, Z + H, i+1);
      }
    break;
    }
  }
}

int mode4(){ // in development

}


//-------------------------------------------------------IK------------------------------------------------------------
int IK(float y, float x, float z, int leg )
{
  float x0; // x rotation placeholder
  float y0; // y rotation placeholder

  // offsets and rotation matrixes
  switch(leg)
  {
    case 1: {y -= 64; x -= 98; x0 = x; y0 = y;
    x = x0*cos(PI/4) - y0*sin(PI/4);
    y = x0*sin(PI/4) + y0*cos(PI/4);
    break;}
    case 2: {y -= 81; x -= 0; break;}
    case 3: { y -= 64; x -= -98; x0 = x; y0 = y;
    x = x0*cos(7*PI/4) - y0*sin(7*PI/4);
    y = x0*sin(7*PI/4) + y0*cos(7*PI/4);
    break;}
    case 4: {y -= -64; x -= -98; y *= -1; x *= -1; x0 = x; y0 = y;
    x = x0*cos(PI/4) - y0*sin(PI/4);
    y = x0*sin(PI/4) + y0*cos(PI/4);
    break;}
    case 5: {y -= -81; x -= 0; y *= -1; x *= -1;  break;}
    case 6: {y -= -64; x -= 98; y *= -1; x *= -1; x0 = x; y0 = y;
    x = x0*cos(7*PI/4) - y0*sin(7*PI/4);
    y = x0*sin(7*PI/4) + y0*cos(7*PI/4);
    break;}
  }

  // IK equations
  float d = sqrt(x * x + y * y);
  float r = d - l;
  float c = sqrt(z * z + r * r);

  // Angles in degrees
  float theta1 = atan2(y, x) * 180.0 / PI;
  float theta2 = atan2(r,-z) * 180.0 / PI + acos((a * a + c * c - b * b) / (2 * a * c)) * 180.0 / PI;
  float theta3 = 180.0 - acos((a * a + b * b - c * c) / (2 * a * b)) * 180.0 / PI;
  //Serial.print("coxaT: "); Serial.println(theta1);
  //Serial.print("femurT: "); Serial.println(theta2);
  //Serial.print("tibiaT: "); Serial.println(theta3);

  // angles to write
  float coxaA;
  float femurA;
  float tibiaA;

  // femur and tibia flip based on right or left legs
  if(leg <=3){
  coxaA = theta1;
  femurA =  180.0 - theta2;
  tibiaA = 180.0 - theta3;
  writeAngles(coxaA, femurA, tibiaA, leg);
  //Serial.print("coxaA: "); Serial.println(coxaA);
  //Serial.print("femurA: "); Serial.println(femurA);
  //Serial.print("tibiaA: "); Serial.println(tibiaA);
  }
  else{
  coxaA = theta1;
  femurA = theta2;
  tibiaA = theta3;
  writeAngles(coxaA, femurA, tibiaA, leg);
  }
}
//-------------------------------------------------------writeAngles---------------------------------------------------
int writeAngles(float C, float F, float T, int leg)
{
  switch(leg){
    case 1:
    {
      pwm1.setPWM(15, 0, map(C, 0, 180, minPulses[0], maxPulses[0]) );
      pwm1.setPWM(14, 0, map(F, 0, 180, minPulses[1], maxPulses[1]) );
      pwm1.setPWM(13, 0, map(T, 0, 180, minPulses[2], maxPulses[2]) );
      break;
    }
    case 2:
    {
      pwm1.setPWM(10, 0, map(C, 0, 180, minPulses[3], maxPulses[3]) );
      pwm1.setPWM(9, 0, map(F, 0, 180, minPulses[4], maxPulses[4]) );
      pwm1.setPWM(8, 0, map(T, 0, 180, minPulses[5], maxPulses[5]) );
      break;
    }
    case 3:
    {
      pwm1.setPWM(2, 0, map(C, 0, 180, minPulses[6], maxPulses[6]) );
      pwm1.setPWM(1, 0, map(F, 0, 180, minPulses[7], maxPulses[7]) );
      pwm1.setPWM(0, 0, map(T, 0, 180, minPulses[8], maxPulses[8]) );
      break;
    }
    case 4:
    {
      pwm2.setPWM(13, 0, map(C, 0, 180, minPulses[9], maxPulses[9]) );
      pwm2.setPWM(14, 0, map(F, 0, 180, minPulses[10], maxPulses[10]) );
      pwm2.setPWM(15, 0, map(T, 0, 180, minPulses[11], maxPulses[11]) );
      break;
    }
    case 5:
    {
      pwm2.setPWM(5, 0, map(C, 0, 180, minPulses[12], maxPulses[12]) );
      pwm2.setPWM(6, 0, map(F, 0, 180, minPulses[13], maxPulses[13]) );
      pwm2.setPWM(7, 0, map(T, 0, 180, minPulses[14], maxPulses[14]) );
      break;
    }
    case 6:
   {
      pwm2.setPWM(0, 0, map(C, 0, 180, minPulses[15], maxPulses[15]) );
      pwm2.setPWM(1, 0, map(F, 0, 180, minPulses[16], maxPulses[16]) );
      pwm2.setPWM(2, 0, map(T, 0, 180, minPulses[17], maxPulses[17]) );
      break;
    }
  }
}
//------------------------------------------------------legSwingC------------------------------------------------------
int legSwingC(int legID) {

  legID--;
  int R = 40;
  int Y;
  int Z;

  if (millis() - lastStep[legID] >= stepDelay && (data.joystick_x > 132)){

    // ---------------- SEMICIRCLE ----------------
    if (state[legID] == 1){

      Y = i[legID];
      Z = sqrt(R * R - Y * Y);

      i[legID]+= 4;

      if (i[legID] == 40)
      state[legID] = 2;

      lastStep[legID] = millis();
      IK(pointsX[legID], pointsY[legID] + Y, -90 + Z, legID + 1);
    }

    // ---------------- STRAIGHT LINE ----------------
    else if (state[legID] == 2){

      Y = i[legID];
      Z = 0;

      i[legID]-= 8;
      
      if (i[legID] == -40)
        state[legID] = 1;

      lastStep[legID] = millis();

      IK(pointsX[legID], pointsY[legID] + Y, -90 + Z, legID + 1);
    }
  }
  if (millis() - lastStep[legID] >= stepDelay && (data.joystick_x < 120)){

    // ---------------- SEMICIRCLE ----------------
    if (state[legID] == 1){

      Y = i[legID];
      Z = sqrt(R * R - Y * Y);

      i[legID]-= 4;

      if (i[legID] == -40)
      state[legID] = 2;

      lastStep[legID] = millis();
      IK(pointsX[legID], pointsY[legID] + Y, -90 + Z, legID + 1);
    }

    // ---------------- STRAIGHT LINE ----------------
    else if (state[legID] == 2){

      Y = i[legID];
      Z = 0;

      i[legID]+= 8;
      
      if (i[legID] == 40)
        state[legID] = 1;

      lastStep[legID] = millis();

      IK(pointsX[legID], pointsY[legID] + Y, -90 + Z, legID + 1);
    }
  }




    if (millis() - lastStep[legID] >= stepDelay && (data.joystick_y > 132)){

    // ---------------- SEMICIRCLE ----------------
    if (state[legID] == 1){

      Y = i[legID];
      Z = sqrt(R * R - Y * Y);

      i[legID]+= 1;

      if (i[legID] == 40)
      state[legID] = 2;

      lastStep[legID] = millis();
      IK(pointsX[legID] + Y, pointsY[legID], -90 + Z, legID + 1);
    }

    // ---------------- STRAIGHT LINE ----------------
    else if (state[legID] == 2){

      Y = i[legID];
      Z = 0;

      i[legID]-= 1;
      
      if (i[legID] == -40)
        state[legID] = 1;

      lastStep[legID] = millis();

      IK(pointsX[legID] + Y, pointsY[legID], -90 + Z, legID + 1);
    }
  }
  if (millis() - lastStep[legID] >= stepDelay && (data.joystick_y < 120)){

    // ---------------- SEMICIRCLE ----------------
    if (state[legID] == 1){

      Y = i[legID];
      Z = sqrt(R * R - Y * Y);

      i[legID]-= 1;

      if (i[legID] == -40)
      state[legID] = 2;

      lastStep[legID] = millis();
      IK(pointsX[legID] + Y, pointsY[legID], -90 + Z, legID + 1);
    }

    // ---------------- STRAIGHT LINE ----------------
    else if (state[legID] == 2){

      Y = i[legID];
      Z = 0;

      i[legID]+= 1;
      
      if (i[legID] == 40)
        state[legID] = 1;

      lastStep[legID] = millis();

      IK(pointsX[legID] + Y, pointsY[legID], -90 + Z, legID + 1);
    }
  }

  lastMode = 2;
}

int startAnim(){ // first frame
  IK(240, 98, 20, 1);
  IK(240, 0, 20, 2);
  IK(240, -98, 20, 3);
  IK(-240, -98, 20, 4);
  IK(-240, 0, 20, 5);
  IK(-240, 98, 20, 6);
  delay(1000);   //second frame
  IK(190, 190, 0, 1);
  IK(220, 0, 0, 2);
  IK(190, -190, 0, 3);
  IK(-190, -190, 0, 4);
  IK(-220, 0, 0, 5);
  IK(-190, 190, 0, 6);
  delay(1000);   //push up frames sequence
  for(int i = 0; i >= -70; i -= 5)
{
  IK(175, 175, i, 1);
  IK(210,   0, i, 2);
  IK(175, -175, i, 3);
  IK(-175,-175, i, 4);
  IK(-210,  0, i, 5);
  IK(-175, 175, i, 6);
  delay(5);
}
delay(1000);
}

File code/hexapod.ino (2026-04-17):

#include <SPI.h>
#include <nRF24L01.h>
#include <RF24.h>
#include <Wire.h>
#include <Adafruit_PWMServoDriver.h>
#include <FastLED.h>
//IK
int legID;

int OffsetX; //leg position X offset
int OffsetY; //leg potion Y offset
int OffsetA; // angle offset

const int CoxaL = 44; // coxa lenght
const int FemurL = 60; // femur lenght
const int TibiaL = 107; // tibia lenght

//PINS
const int relay1 = 4;
const int relay2 = 7;

//VARIABLES
int light;

//start anim controller
bool startDone = false;

//-------------------------------LED NIGHTLIGHT-----------------------------------------------

CRGB leds1[5];
CRGB leds2[5];

//----------------------------Servo driver settings-------------------------------------------

Adafruit_PWMServoDriver pwm1 = Adafruit_PWMServoDriver(0x40); //servo driver setup
Adafruit_PWMServoDriver pwm2 = Adafruit_PWMServoDriver(0x41);
#define SERVOMINcoxa  125
#define SERVOMAXcoxa  575
#define SERVOMINfemur  125
#define SERVOMAXfemur  575
#define SERVOMINtibia  125
#define SERVOMAXtibia  575

//----------------------------------NRF SETTINGS----------------------------------------------

RF24 radio(8, 9); // CE, CSN

const byte address[6] = "00001";

unsigned long lastReceiveTime = 0;
unsigned long currentTime = 0;

struct Data_Package { // data package sent to hexapod
  byte mode;
  byte height;
  byte joystick_x;
  byte joystick_y;
  byte joystick_select;
  byte option;
};
Data_Package data; //Create a variable with the above structure

struct Gait_creator { // data package sent to hexapod
  int time1;
  int time2;
  int time3;
  int time4;
  int time5;
  int time6;
};

//---------------------------------------GAIT TYPES------------------------------------------

Gait_creator trypod;

//////////////////////////////////////////SETUP///////////////////////////////////////////////

void setup() 
{
  Serial.begin(9600);

  FastLED.addLeds<WS2812B, 5, GRB>(leds1, 5);    //-----FAST LED
  FastLED.addLeds<WS2812B, 6, GRB>(leds2, 5);
  FastLED.setMaxPowerInVoltsAndMilliamps(5, 500);
  FastLED.setBrightness(60);
  FastLED.clear();
  FastLED.show();

  radio.begin();                                 //----NRF transmission setup
  radio.openReadingPipe(0, address);
  radio.setPALevel(RF24_PA_LOW);
  radio.startListening();
  
  pwm1.begin();                                  //-----servo driver setup
  pwm2.begin();
  pwm1.setPWMFreq(60);
  pwm2.setPWMFreq(60);
  yield();

//-----------------------------------------PIN SETUP----------------------------------------------

  pinMode(relay1, OUTPUT);
  pinMode(relay2, OUTPUT);
  pinMode(10, OUTPUT); // for proper NRF behavior
  digitalWrite(4, LOW);
  digitalWrite(7, LOW);

}

////////////////////////////////////////////////LOOP//////////////////////////////////////////////////

//----------------------------------------------Light sensor check/start anim-------------------------------------------
void loop()
{
  if (!startDone) {                    //start anim
    delay(500);
    startAnim();
    startDone = true;
  }                                   //light check

  light = analogRead(A3);
  //Serial.println(light);
  if (light < 15) {
    for (int i = 0; i < 5; i++) {
      leds1[i] = CRGB(255, 110, 0);
      leds2[i] = CRGB(255, 110, 0);
      FastLED.show();
    }
  }
  else {
    for (int i = 0; i < 5; i++) {
      leds1[i] = CRGB(0, 0, 0);
      leds2[i] = CRGB(0, 0, 0);
      FastLED.show();
    }
  }

//------------------------------------NRF COMMUNICATION----------------------------------------------

  if (radio.available())                    //read radio and reset data if connection is lost, prevent locking into a movement
  {if (radio.available())
{
  radio.read(&data, sizeof(Data_Package));  // read struct directly
  lastReceiveTime = millis();

  // Debug print
  //Serial.print("Mode: "); Serial.println(data.mode);
  //Serial.print("Height: "); Serial.println(data.height);
  //Serial.print("Joy X: "); Serial.println(data.joystick_x);
  //Serial.print("Joy Y: "); Serial.println(data.joystick_y);
  //Serial.print("Joy Btn: "); Serial.println(data.joystick_select);
  //Serial.print("Option: "); Serial.println(data.option);
}
  }
  currentTime = millis();

  if ( currentTime - lastReceiveTime > 1000 ) 
  {
    //innitial controller values
    data.mode = 1; //mode selection
    data.height = 127; // height offset
    data.joystick_x = 127;
    data.joystick_y = 127;
    data.joystick_select = 0; // joystick button
    data.option = 1; // the option for the current mode (1-3)
  }

 selectMode();
}

void startAnim()
{

}

void selectMode(){
  switch(data.mode){
  case 1: walkMode(); break;
  case 2: crabMode(); break;
  case 3: bodymovementMode(); break;
  case 4: animationMode(); break;
 }
}

void walkMode()
{
  switch(data.option){
    case 1: ; break;
    case 2: ; break;
    case 3: ; break;
  }
}

void crabMode()
{
  switch(data.option){
    case 1: ; break;
    case 2: ; break;
    case 3: ; break;
  }
}

void bodymovementMode()
{
  switch(data.option){
    case 1: ; break;
    case 2: ; break;
    case 3: ; break;
  }
}

void animationMode()
{
  if(data.joystick_y > 200){
    switch(data.option){
      case 1: ; break;
      case 2: ; break;
      case 3: ; break;
    }
  }

}

void IK()
{

}

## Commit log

2026-04-17 Update and rename test to BOM link
2026-04-17 Update BOM link
2026-04-17 Update and rename BOM link to BOM link.txt
2026-04-17 Rename BOM link.txt to BOM link
2026-04-17 Rename cap x18.stl to friction cap x18.stl
    [friction cap x18.stl]
2026-04-17 Rename servo order.png to servo_order.png
